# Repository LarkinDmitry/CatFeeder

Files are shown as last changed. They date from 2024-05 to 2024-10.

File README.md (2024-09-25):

# CatFeeder
Данный проект позволит вам собрать автоматическую кормушку для ваших домашних животных.
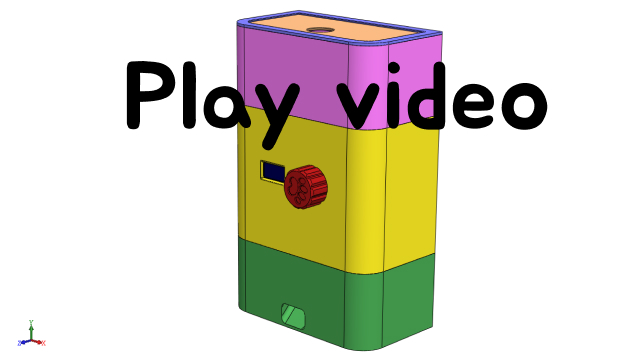
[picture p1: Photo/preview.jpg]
(https://www.youtube.com/watch?v=flGAjXiUZWA)


## Особенности этой кормушки:
* Для работы кормушки необходим обычный блок питания 5V. Ток не менее 2A (лучше 3A);
* Кормушку можно запитать от обычного павербанка;
* В кормушке применен модуль часов реального времени, это позволяет не переживать за возможные перебои с электричеством;
* В режиме ожидания кормушка показывает текущее время;
* Программа позволяет настраивать до 7 сеансов кормления в сутки (без перепрошивки контроллера);
* Вы сможете настроить время и количество корма для каждого сеанса;
* Настройки сохраняются в энергонезависимой памяти;
* При отсутствии электричества в момент очередного сеанса кормления, этот сеанс пропускается. При восстановлении электричества кормушка продолжит свою работу;
* Детали оптимизированы под печать PETG пластиком на FDM принтере с областью печати 200х200х200мм;
* Предусмотрено крепление кормушки на стену.

## Порядок сборки:
* Рекомендую с начала полностью прочитать статью и только после этого приступать к сборке.

### Электронная часть
* Подготовьте следующий список необходимых компонентов:
  - Повышающий DC-DC модуль XL6009;
  - модуль часов реального времени DS3231;
  - Arduino nano;
  - Шаговый двигатель 17HS4401 (или аналог. Высота корпуса двигателя не должна превышать 42мм, иначе он не залезет в корпус)
  - драйвер шагового двигателя A4988 (использование тихих драйверов типа TMC пойдет во вред, т.к. дополнительные вибрации во время работы двигателя помогают подаче корма);
  - I2C OLED 0.96" дисплей 128x64;
  - Модуль поворотного энкодера HW-040 (KY-040);
  - Макетная плата 5x7cm;
  - Электролитический конденсатор 16В 100uF;
  - Гнездо type-c;
  - Соединительные провода.
* Залейте на Arduino nano прошивку из папки [Arduino/catFeeder](https://github.com/LarkinDmitry/CatFeeder/tree/main/Arduino/catFeeder);
* Распаяйте контакты на arduino nano так как показано на фото ниже;

* Настройте выходное напряжение на модуле XL6009 равное 12В;
* Распаяйте все компоненты на макетной плате  так как показано на фото ниже;

* Соедините все контакты компонентов дорожками в соответствии с картинкой ниже. Установите модуль часов реального времени DS3231 и драйвер шагового двигателя A4988; 

* Подключите питание к контактам IN+/IN- модуля XL6009 и настройте ток на драйвере шагового двигателя равным 0,5А (Vref = 0.4В). Большой крутящий момент в данном проекте не требуется, алгоритм вращения фидерного колеса позволяет справляться с закусыванием корма при подаче. !!! Внимание !!! не используйте в качестве источника питания USB порт компьютера, он не сможет выдать необходимый ток;
* Подключите дисплей, энкодер и шаговый двигатель;
* Проверьте работоспособность собранной платы.

### Механическая часть
* Распечатайте все детали из папки [3DModels/STL](https://github.com/LarkinDmitry/CatFeeder/tree/main/3DModels/STL). Если необходимо внести изменения, в папке [3DModels](https://github.com/LarkinDmitry/CatFeeder/tree/main/3DModels) есть исходные файлы для SOLIDWORKS 2018;
* Соедините детали корпуса как показано на фото 1 и 2 ниже. Если необходимо увеличить объем бака с кормом, вы можете еще раз распечатать деталь "L.013.00.00.04 Tank" и установить ее (фото 3).

* Скрепите детали крышки, используя 2 кусочка филамента длинной 17,5мм и диаметром 1,75мм;

* Установите крышку на корпус;

* Возьмите 4 винта M3x10 и закрепите ими шаговый двигатель 17HS4401. Установите фидерное колесо на шток двигателя. Колесо должно плотно сидеть на валу исключая прокручивание;

* Установите гнездо type-c в нижнюю часть корпуса и припаяйте провода к контактам IN+/IN- модуля XL6009;

* С помощью термоклея закрепите на верхней части корпуса, дисплей и энкодер. Рекомендую предварительно припаять соединительные провода к контактам;

* Подключите шаговый двигатель, энкодер и дисплей к плате управления. Установите плату управления в специальные пазы внутри нижней части корпуса. Подключите питание и проверьте работоспособность;

* Используя саморезы 3,5х25 скрепите между собой верхнюю и нижнюю части корпуса, саморезы устанавливайте через отверстия в дне нижней части корпуса;

* Повторно проверьте работоспособность. Поздравляю, сборка завершена!

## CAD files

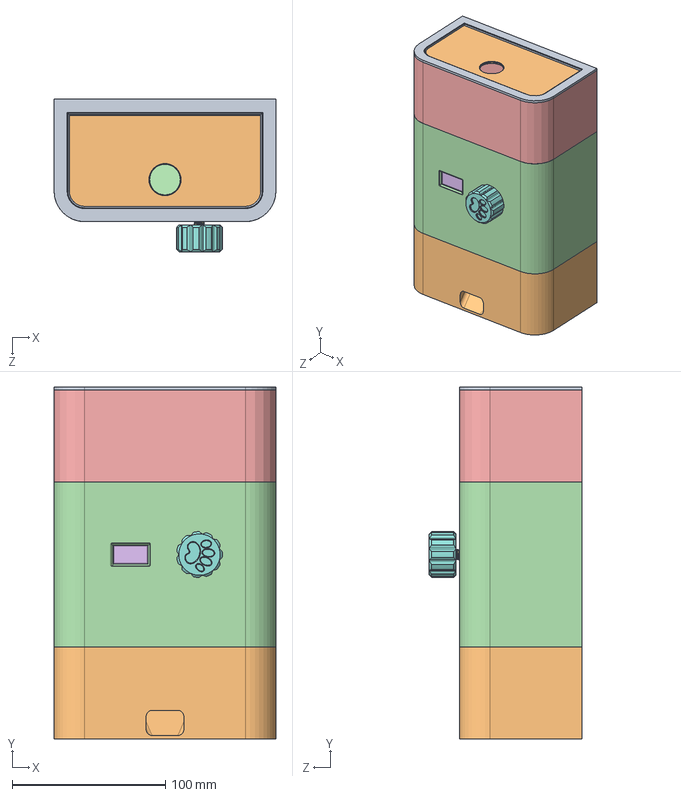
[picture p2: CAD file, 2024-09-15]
3DModels/L.013.00.00.00 Cat feeder.SLDASM
145.0 x 230.0 x 99.7 mm
NEMA 17HS13-0404S1
L.013.00.00.01 BodyBottom
L.013.00.00.02 Wheel
L.013.00.00.03 BodyTop
L.013.00.00.04 Tank
OLED-128x64-0.96
Rotary Encoder - KY-040
L.013.00.00.05 Knob
L.013.00.00.06 CapFrame
L.013.00.00.07 Cap

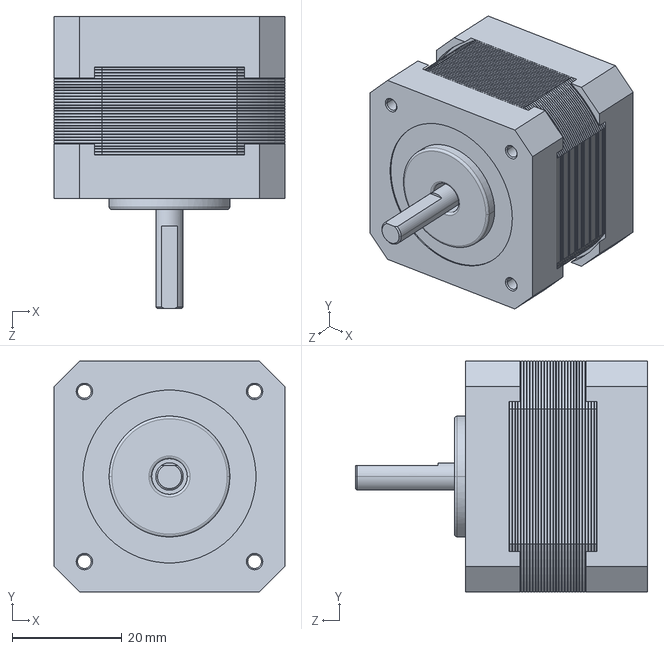
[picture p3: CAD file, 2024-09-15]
3DModels/NEMA 17HS13-0404S1.SLDPRT
42.0 x 42.0 x 53.2 mm

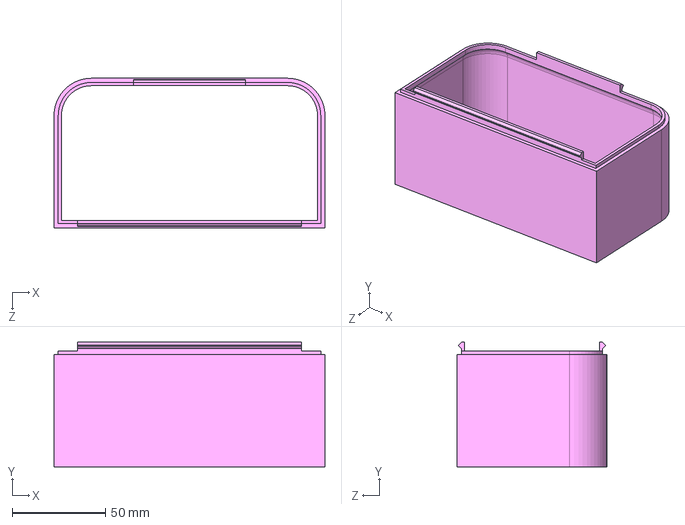
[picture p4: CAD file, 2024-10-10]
3DModels/STEP/L.013.00.00.04 Tank.STEP
145.0 x 66.7 x 80.0 mm

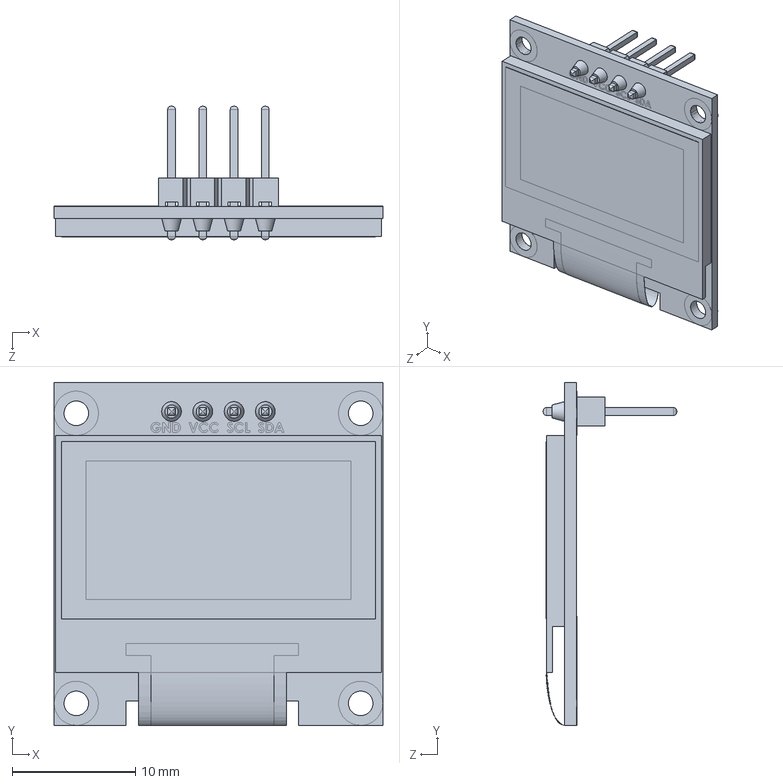
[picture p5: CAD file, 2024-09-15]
3DModels/OLED-128x64-0.96.SLDPRT
26.7 x 27.9 x 10.8 mm

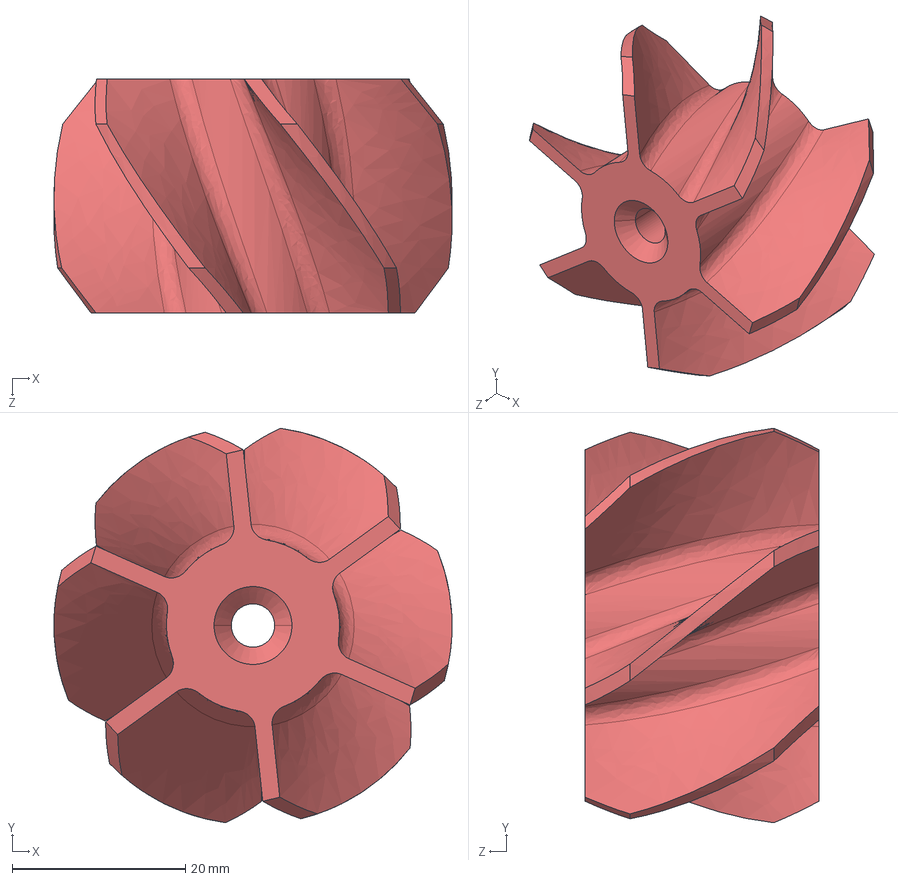
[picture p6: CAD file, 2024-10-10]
3DModels/STEP/L.013.00.00.02 Wheel.STEP
46.0 x 45.6 x 27.0 mm

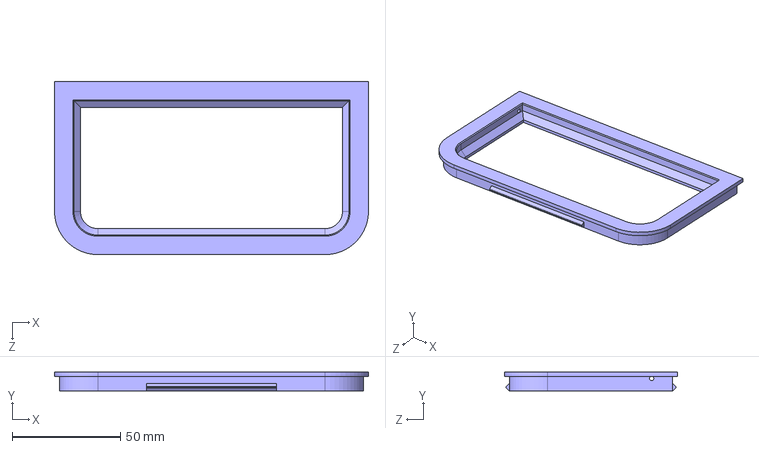
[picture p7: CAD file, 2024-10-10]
3DModels/STEP/L.013.00.00.06 CapFrame.STEP
145.0 x 8.70 x 80.0 mm

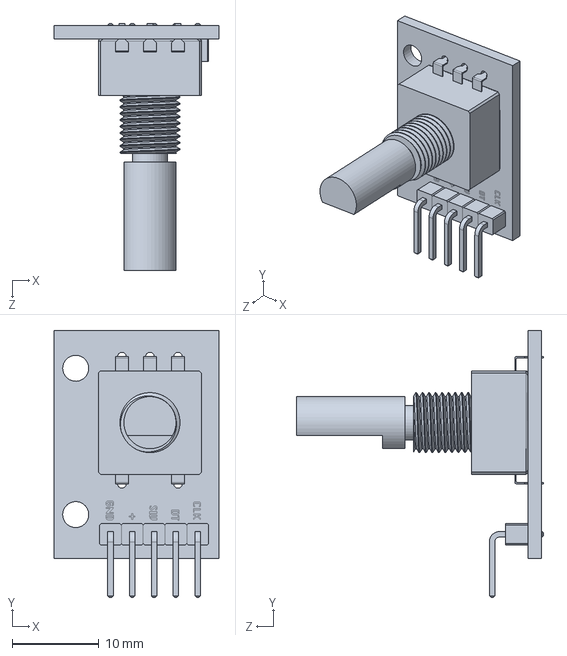
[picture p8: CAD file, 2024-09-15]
3DModels/Rotary Encoder - KY-040.SLDPRT
19.0 x 30.8 x 28.4 mm

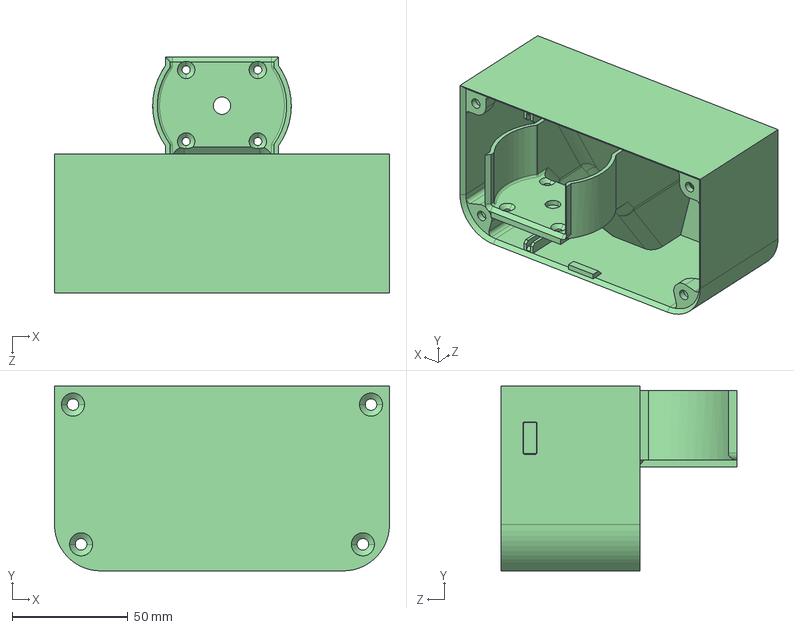
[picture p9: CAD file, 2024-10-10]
3DModels/STEP/L.013.00.00.01 BodyBottom.STEP
145.0 x 80.0 x 102.0 mm

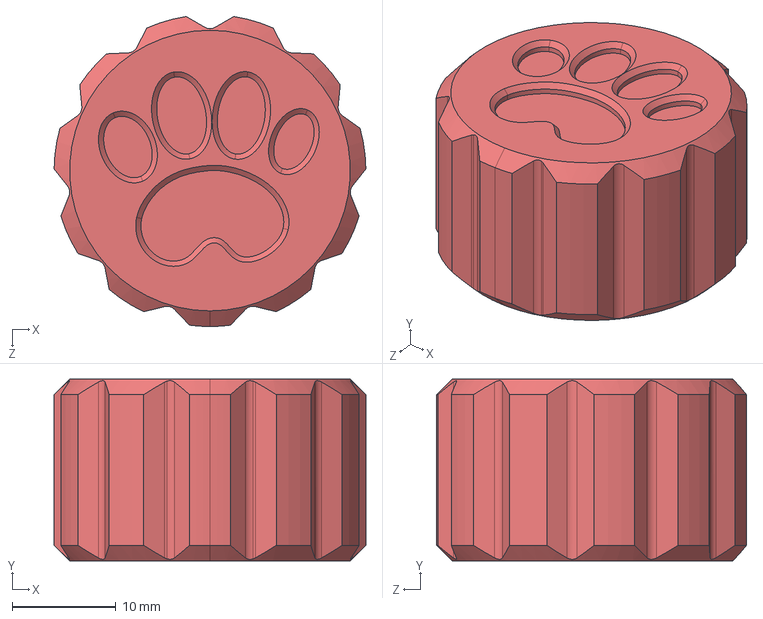
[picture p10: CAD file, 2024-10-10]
3DModels/STEP/L.013.00.00.05 Knob.STEP
30.0 x 17.5 x 29.8 mm

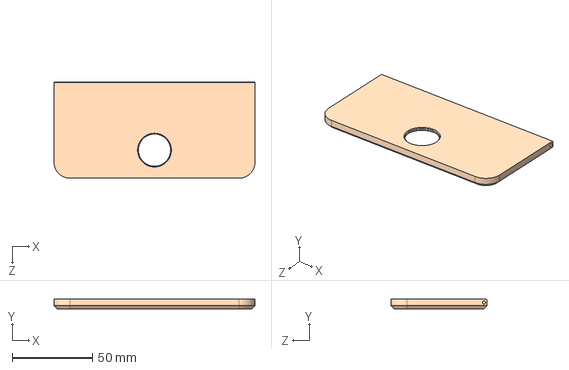
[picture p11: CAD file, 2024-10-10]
3DModels/STEP/L.013.00.00.07 Cap.STEP
125.0 x 6.00 x 60.0 mm

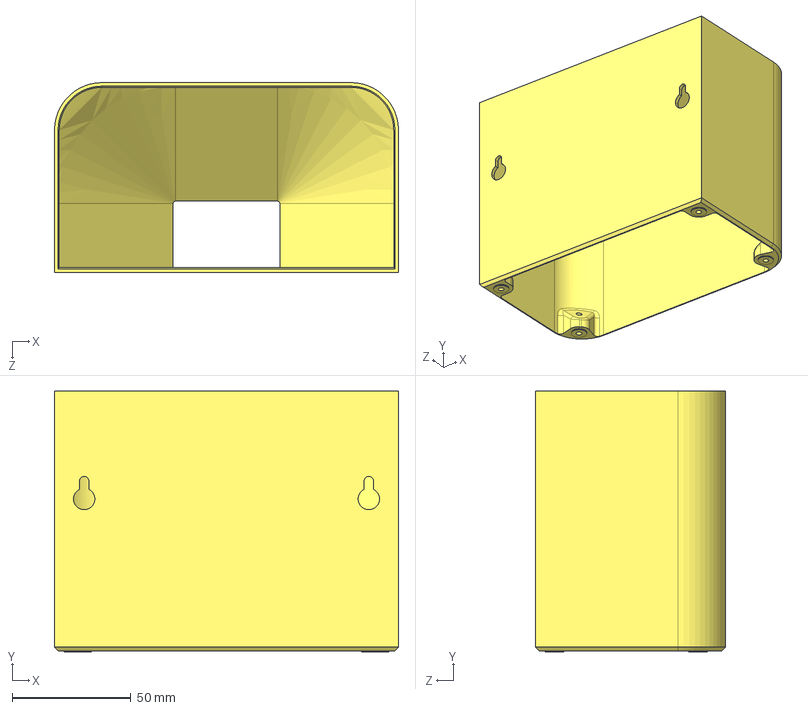
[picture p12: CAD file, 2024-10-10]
3DModels/STEP/L.013.00.00.03 BodyTop.STEP
145.0 x 110.0 x 80.0 mm

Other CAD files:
3DModels/L.013.00.00.01 BodyBottom.SLDPRT
3DModels/L.013.00.00.02 Wheel.SLDPRT
3DModels/L.013.00.00.03 BodyTop.SLDPRT
3DModels/L.013.00.00.04 Tank.SLDPRT
3DModels/L.013.00.00.05 Knob.SLDPRT
3DModels/L.013.00.00.06 CapFrame.SLDPRT
3DModels/L.013.00.00.07 Cap.SLDPRT
3DModels/STL/L.013.00.00.01 BodyBottom.STL
3DModels/STL/L.013.00.00.02 Wheel.STL
3DModels/STL/L.013.00.00.03 BodyTop.STL
3DModels/STL/L.013.00.00.04 Tank.STL
3DModels/STL/L.013.00.00.05 Knob.STL
3DModels/STL/L.013.00.00.06 CapFrame.STL
3DModels/STL/L.013.00.00.07 Cap.STL

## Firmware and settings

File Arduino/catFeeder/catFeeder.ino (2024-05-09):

#include <Arduino.h>
#include "GyverEncoder.h"
#include "view.h"

#define CLK 6
#define DT 7
#define SW 8
Encoder enc(CLK, DT, SW);

View* view;
MainMenuView mainMenuView;
HomeView homeView;
SetTimeView setTimeView;
FeedingListView feedingListView;
FeedingItemMenuView feedingItemMenuView;
FeedingItemSettingsView feedingItemSettingsView;

DateTime lastActionTime;

void setup() {
  Serial.begin(115200);
  enc.setType(TYPE2);
  model.init();
  oled.init();
  oled.clear();
  setScreen(Home);
}

void loop() {
  // обязательные функции отработки. Должны постоянно опрашиваться
  enc.tick();
  view->tick();
  model.tick();
  
  if (enc.isRight()){
    lastActionTime = rtc.getTime();
    view -> turnRight();
  }
  
  if (enc.isLeft()){
    lastActionTime = rtc.getTime();
    view -> turnLeft();
  }
  
  if (enc.isClick()){
    lastActionTime = rtc.getTime();
    setScreen(view -> click());
  }

  checkInactivityTime();
}

void setScreen(ViewScreen screen){
  switch (screen)
  {
  case Home: view = &homeView; resetAllPointers(); break;
  case Main: view = &mainMenuView; break;
  case SetTime: view = &setTimeView; break;
  case FeedingsList: view = &feedingListView; break;
  case FeedingItemMenu: view = &feedingItemMenuView; break;
  case FeedingItemSettings: view = &feedingItemSettingsView; break;
  }
  view -> show();
}

void resetAllPointers(){
  homeView.resetPointer();
  mainMenuView.resetPointer();
  setTimeView.resetPointer();
  feedingListView.resetPointer();
  feedingItemMenuView.resetPointer();
  feedingItemSettingsView.resetPointer();
}

void checkInactivityTime(){
  if(view->screenType != Home){
    if(getDeltaSeconds(lastActionTime, rtc.getTime()) > 30){      
      oled.clear();     
      setScreen(Home);
    }
  }
}

int getDeltaSeconds(DateTime firstDate, DateTime secondDate){
  int firstSeconds = firstDate.hour * 3600 + firstDate.minute * 60 + firstDate.second;
  int secondSeconds = secondDate.hour * 3600 + secondDate.minute * 60 + secondDate.second;
  return secondSeconds - firstSeconds;
}

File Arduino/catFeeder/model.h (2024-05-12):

#include <microDS3231.h>
#include <EEPROM.h>
#include "feeder.h"

MicroDS3231 rtc;
Feeder feeder;

struct FeedingItem
{
  bool isActive = false;
  int8_t hour = 0;
  int8_t minute = 0;
  int8_t portions = 0;

  int portionsNow(DateTime now){
    if(isActive && now.hour == hour && now.minute == minute){
      return portions;
    }
    else{
      return 0;
    }
  }
};

struct FeedingsListData
{
  uint8_t checkValue0 = 0;
  uint8_t checkValue255 = 255;
  uint8_t listLength = 7;
  FeedingItem feedingList[7];
};

class Model{
  public:
  Model(){};

  int selectedItem = 0;
  int readyPortions = 0;
  FeedingsListData feedingData;

  void init(){
    EEPROM.get(0, feedingData);

    // first start check
    if(feedingData.checkValue0 != 0 || feedingData.checkValue255 != 255){
      FeedingsListData defData;
      EEPROM.put(0, defData);
      EEPROM.get(0, feedingData);
    }
  }

  void clearSelectedItem(){
    feedingData.feedingList[selectedItem].isActive = false;
    feedingData.feedingList[selectedItem].hour = 0;
    feedingData.feedingList[selectedItem].minute = 0;
    feedingData.feedingList[selectedItem].portions = 0;
    EEPROM.put(0, feedingData);
  }

  FeedingItem getSelectedItem(){
    return feedingData.feedingList[selectedItem];
  }

  void saveSelectedItem(FeedingItem item){
    feedingData.feedingList[selectedItem] = item;
    EEPROM.put(0, feedingData);
  }

  void tick(){
    DateTime now = rtc.getTime();
    if(lastCheckTime.second != now.second){
      lastCheckTime = now;
      if(now.second == 0){
        for(int i = 0; i < feedingData.listLength; i++){
          int j = feedingData.feedingList[i].portionsNow(now);
          readyPortions += j;
        }
      }
    }

    if(readyPortions > 0){
      feeder.givePortions(readyPortions);
      readyPortions = 0;
    }

    feeder.tick();
  }

  private:
  DateTime lastCheckTime;
};
Model model;

String getHHMM(){
  String time = "";
  if(rtc.getHours() < 10) time += String(0, DEC);
  time += String(rtc.getHours(), DEC) + ":";
  if(rtc.getMinutes() < 10) time += String(0, DEC);
  time += String(rtc.getMinutes(), DEC);
  return time;
}

String feedingItemToString(FeedingItem item){
  String str = "";
  if(item.isActive){
    if(item.hour < 10) str += String(0, DEC);
    str += String(item.hour, DEC) + ":";
    if(item.minute < 10) str += String(0, DEC);
    str += String(item.minute, DEC) + " - ";
    if(item.portions < 10) str += String(0, DEC);
    str += String(item.portions, DEC) + " порц.";
  }
  else{
    str = "---";
  }
  return str;
}

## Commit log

2024-05-03 start git
    [L.013.00.00.00 Cat feeder.SLDASM, L.013.00.00.01 BodyBottom.SLDPRT, L.013.00.00.02 Wheel.SLDPRT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]
2024-05-09 add screen reset when inactive
    [catFeeder.ino]
2024-05-12 optimization 3D models
    [L.013.00.00.00 Cat feeder.SLDASM, L.013.00.00.01 BodyBottom.SLDPRT, L.013.00.00.02 Wheel.SLDPRT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]
2024-09-15 pin switch
2024-09-15 added video preview
    [L.013.00.00.05 Knob.SLDPRT]
2024-09-15 optimization 3D models, added .stl
    [L.013.00.00.00 Cat feeder.SLDASM, L.013.00.00.01 BodyBottom.STL, L.013.00.00.02 Wheel.STL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]
2024-10-10 add .step
    [L.013.00.00.01 BodyBottom.STEP, L.013.00.00.02 Wheel.STEP, L.013.00.00.03 BodyTop.STEP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]
